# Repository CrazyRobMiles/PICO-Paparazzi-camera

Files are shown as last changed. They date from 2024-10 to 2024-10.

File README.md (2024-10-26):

# PICO-Paparazzi-camera
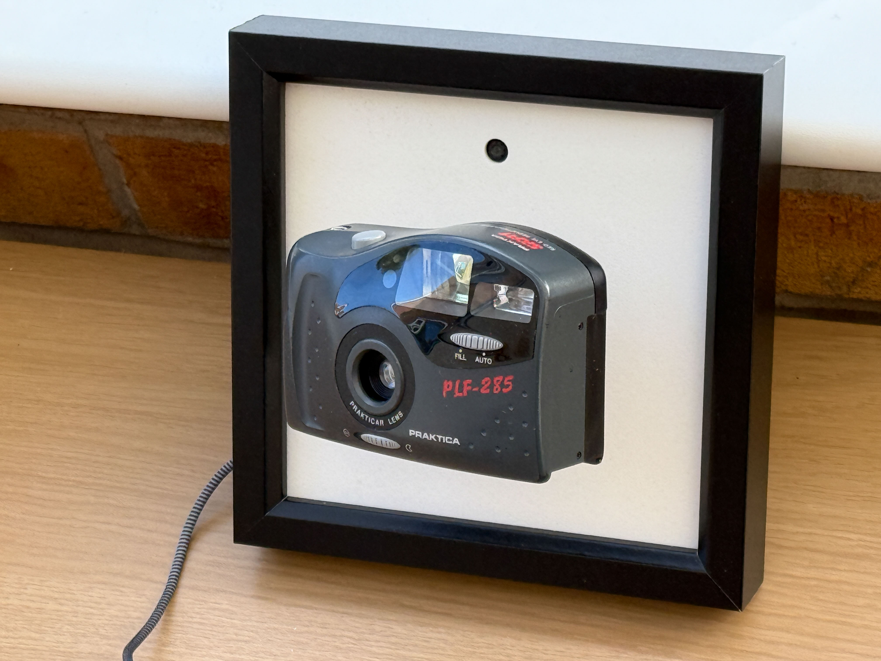
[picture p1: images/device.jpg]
Point and shoot camera floating above a picture frame

A camera that follows you around the room. Most of the time. 

This project started with a simple idea and then I found ways to make it more complicated. I had a lot of broken film cameras and 
I wanted to make something that made one follow me round the room. I found a sensor that can detect the position of people 
in front of it, and I started with a Raspberry Pi PICO and some servos to see if I could make something which pointed the 
servos at person. I called it the Paparazzi camera. If it went well the next step would be to make a larger 
installation with lots of cameras. It's been an interesting ride, and I'm still not sure if I've properly arrived, but it turns out 
that you can have a lot of fun with this stuff either way. The project is a work in progress and I've been through several iterations.
## Pan and tilt
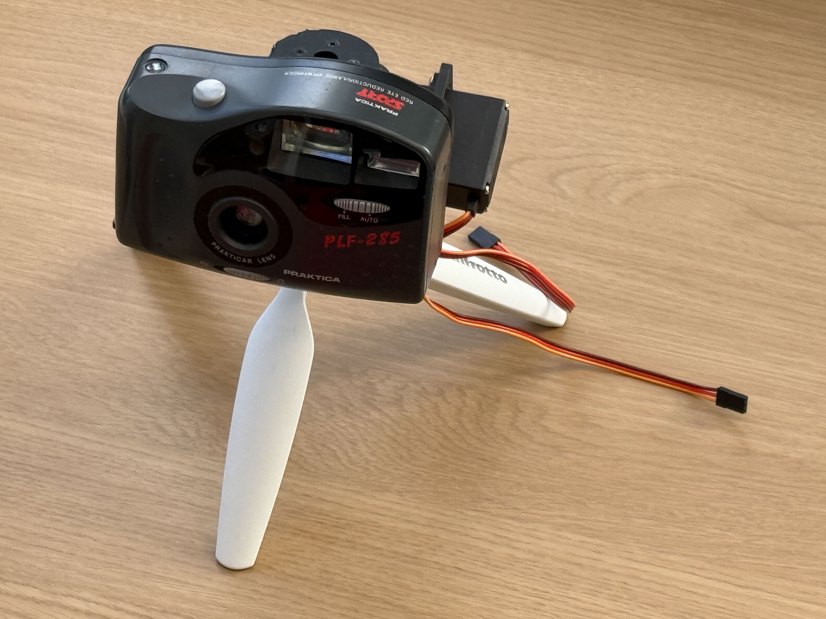
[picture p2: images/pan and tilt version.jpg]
pan and tilt mechanism


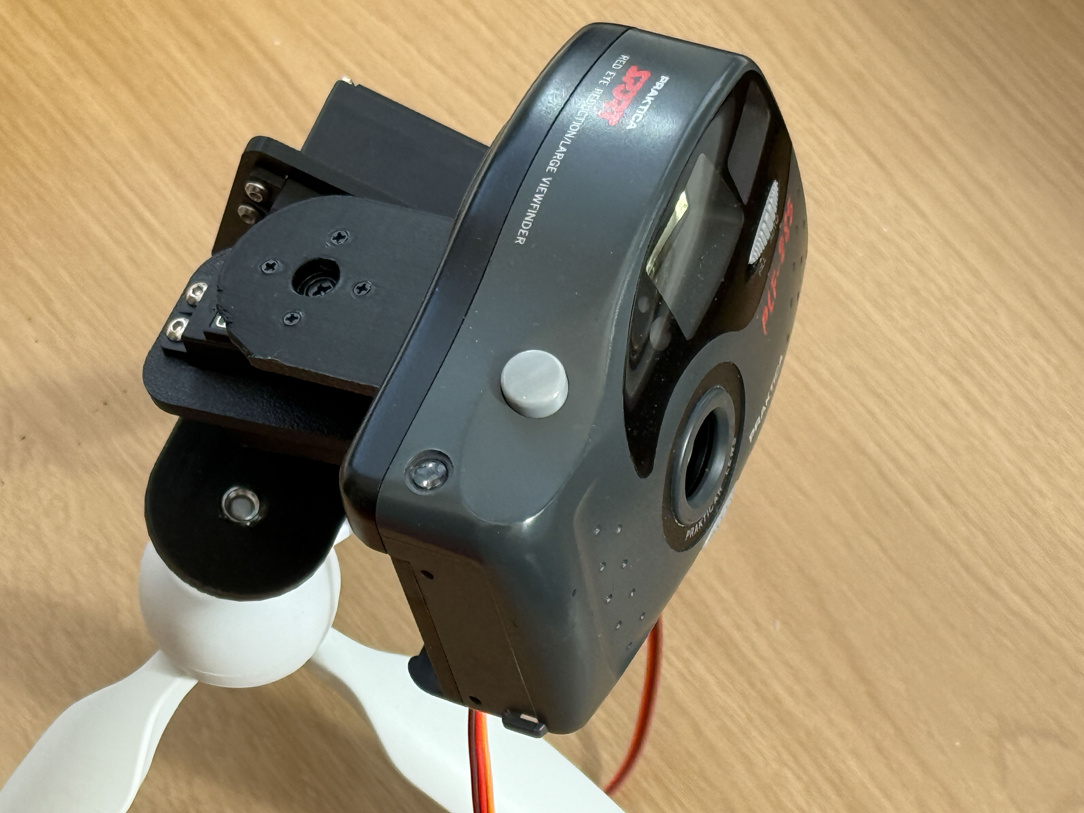
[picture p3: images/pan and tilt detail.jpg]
top view of pan and tilt


A pan and tilt mechanism was the first thing I made that could follow you with a camera. It uses two MG995 servos to create a pan and tilt mechanism. The camera rests on a support at the front. The mechanism 
works fine and will also support a smartphone (you can use it to shoot panoramas if you like).

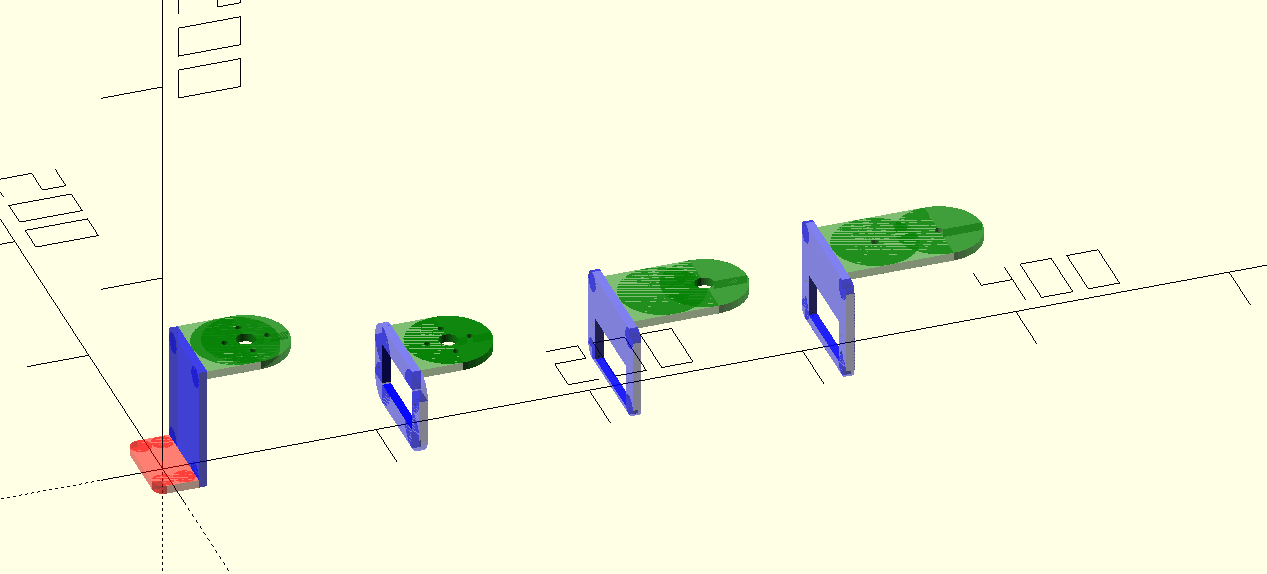
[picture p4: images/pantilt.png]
pan and tilt components

You can find the designs for these components in the 3d printing folder in this repository. Panning and tilting was fun but I really wanted something I could hang on the wall....
## Picture Camera mounting
So I moved on to a wall mounted device inside a six inch square picture frame. These are easy to get hold of from craft shops and are deep enough to allow electronics to be fitted in the back of the frame. Just make sure you get ones with removable glass. 
Some frames have the glass glued in, which makes it very had to remove without breaking it. You can see the picture frame version of the camera in the image at the top of this page. The camera seems to float out of the picture. 
At least, I think it does. 

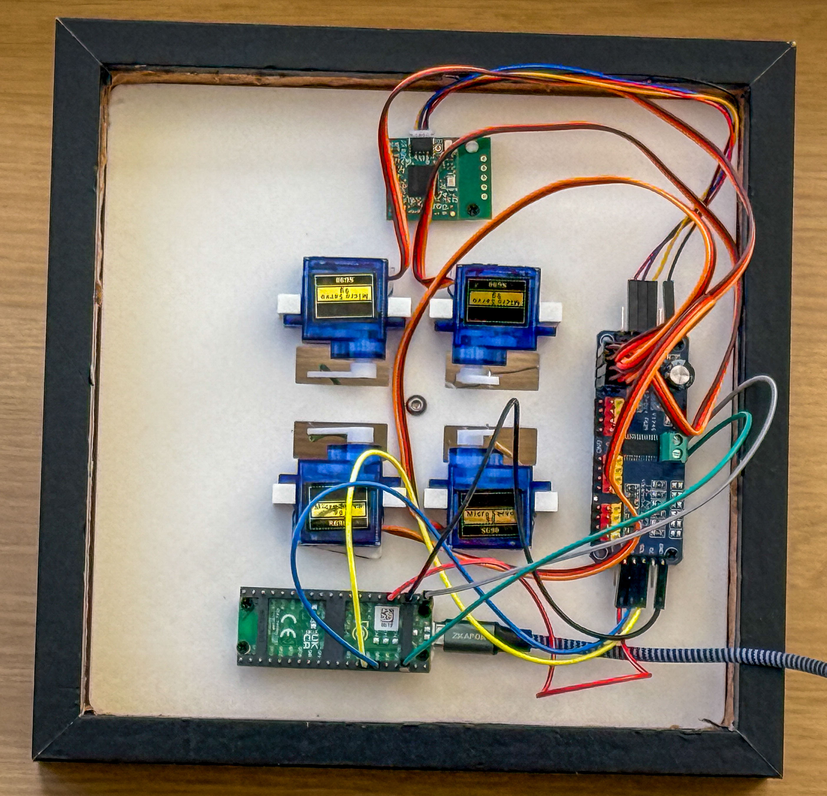
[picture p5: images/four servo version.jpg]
four servo version showing servos


This version uses a picture panel containing four tiny little servos, a Raspberry Pi PICO, a servo driver board and a Useful Sensors [Person sensor](https://github.com/usefulsensors/person_sensor_docs/blob/main/README.md). 

The camera is mounted on 3D printed ball and socket joint which is fitted inside the camera, ideally close to the camera's centre of balance. The idea is that the joint supports the weight of the camera, and the low powered servos only have to move the camera, not support its weight. To make sure there is enough movement force I used four stepper motors rather than two.

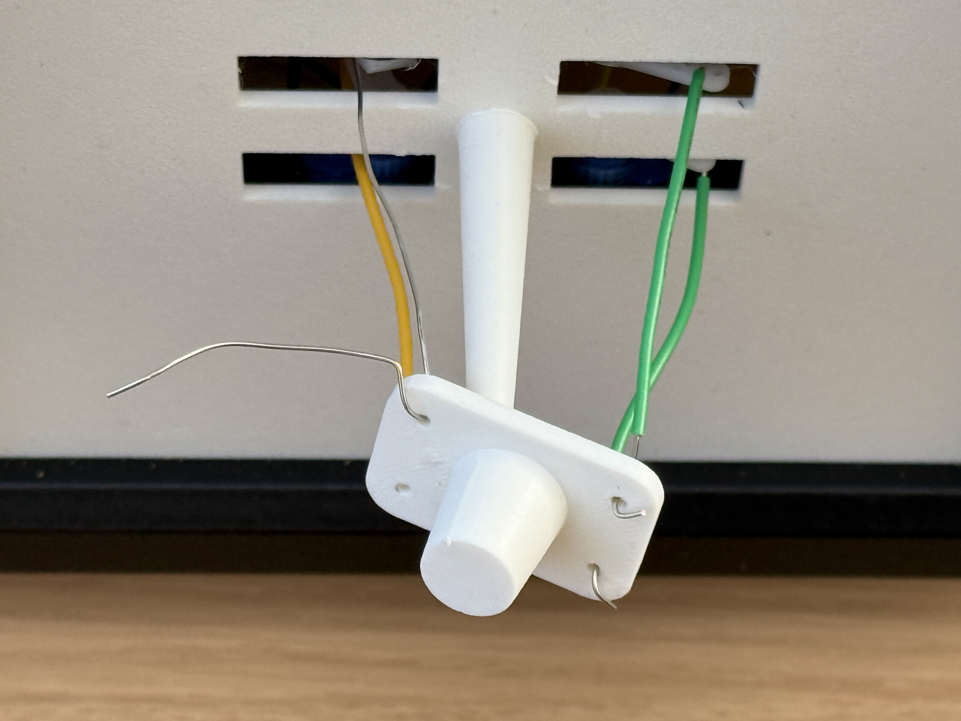
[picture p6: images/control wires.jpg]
control wires linking to the camera support


This shows how the control wires are connected from the servo horns to the camera support. 

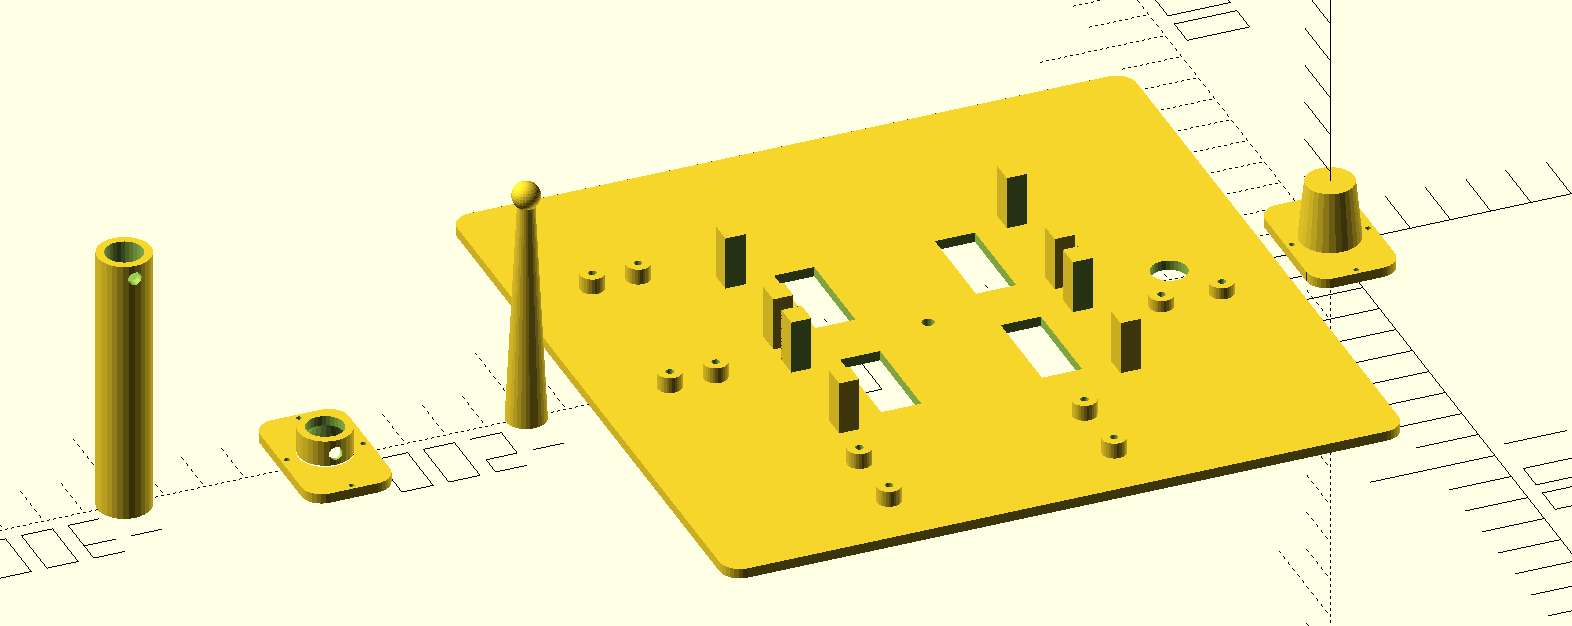
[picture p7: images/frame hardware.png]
3D printed parts for mounting servos


These are the 3D printable parts for the base, camera support pillar and the camera support. The servo motors fit between the support pillars and are glued into place. The camera fitting snaps onto the ball on top of the support. There are pillars to support the other components. There are also versions of the camera plate for a universal joint version of the camera support. The fittings are created by an OpenSCAD script you can find in the 3d printing folder. 

This version works quite well, but it has problems if the camera is not balanced correctly on the end of the support. This causes the camera to twist so that it is not horizontal. It also affects the way that the camera moves. If the camera is not balanced the small servos are unable to lift its weight.

So I thought I'd move on to make a version that uses more powerful servos that can lift the camera weight. I also switched to a universal joint rather than a ball and socket for the camera support. The joint provides pan and tilt motion but not twisting. You can find the universal joints that I used [here](https://www.amazon.co.uk/dp/B09NXJ9QF4).

## Two and Four servos

The four servo design uses SG90 servos. The two servo version of the design uses the same MG995 servos as the original pan and tilt mechanism. These can easily lift the camera up and down, although they are more heavily geared which means that the movement is slightly slower. The two servo backplate design is in the 3d printing folder. 

## Circuitry

The servos are driven by a PCA9685 16 Channel 12-bit PWM Servo motor driver. Both the servo driver board and the person sensor are connected to I2C. This is made easy by the way that the server driver board has i2c pass through. 

### Servo controller connection
The servo controller pins are connected as follows:

* scl GPIO5
* sda GPIO4

The power for the servos is obtained from the VBUS connection. This means that the servos are powered from the PICO USB connection. This is fine for the servos we are using, but if you start to use larger servos, heavier cameras or more servos you might want to consider 

### Servo connection for 2 servos
* Up/down - servo S0
* left/right - servo S1

### Servo connection for 4 servos

* Up - servo S0
* Left - servo S1
* Right - servo S2
* Down - servo S3

### The Person Sensor
The best way to connect the Person Sensor is by using a QWIIC connector brought out to four sockets which to to pins soldered onto the servo driver board. See the picture above for more details. 

The Person Sensor does work, although it can be a bit reticent. You need to make sure that the area where the camera is being used is well it and if clearing the background behind the image viewed by the sensor also improves recognition.

## Software

The software controlling the device is written in Circuit Python. It uses a set of AdaFruit libraries to control the servos. You can find the software and the libraries in the python folder. Just copy the contents of this folder onto the root directory of the storage for the Circuit Python drive which appears when the PICO is connected to the computer. The program is stored in a file called code.py and will run automatically when your PICO is powered up. When it starts up it moves the camera to each corner in turn and then back into the middle. 

### Servo configuration

You can select the servo configuration by changing the value on the first line of the code:
```
number_of_servos = 2
```
The number of servos can be 2 or 4. Any other number will cause an exception to be raised. 

### Paparazzi class

The Paparazzi class creates a PersonSensor object and an appropriate servo driver object. You can then repeatedly update the position of the camera by calling the update method on the Paparazzi instance:
```
pap = Paparazzi(number_of_servos)

while True:
    pap.update()
    time.sleep(0.1)

```
The code above updates the sensor every tenth of a second. You can use the scan method to test all the positions of the servos:

```
pap = Paparazzi(number_of_servos)

pap.scan()
```

This causes the program to scan the camera from left to right and up and down. It is very useful for tuning the lengths of the control wires.

Have fun!

Rob Miles

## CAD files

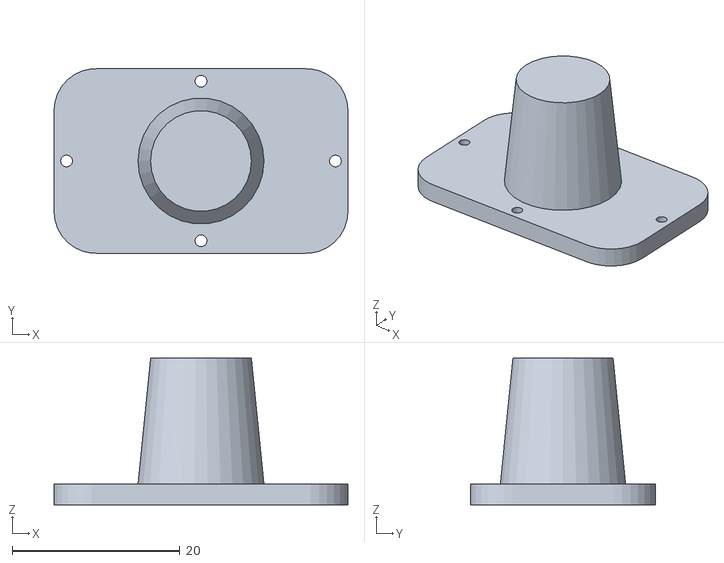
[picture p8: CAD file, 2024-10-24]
3d printing/frame/backplateSocket.stl
35.0 x 22.0 x 17.5

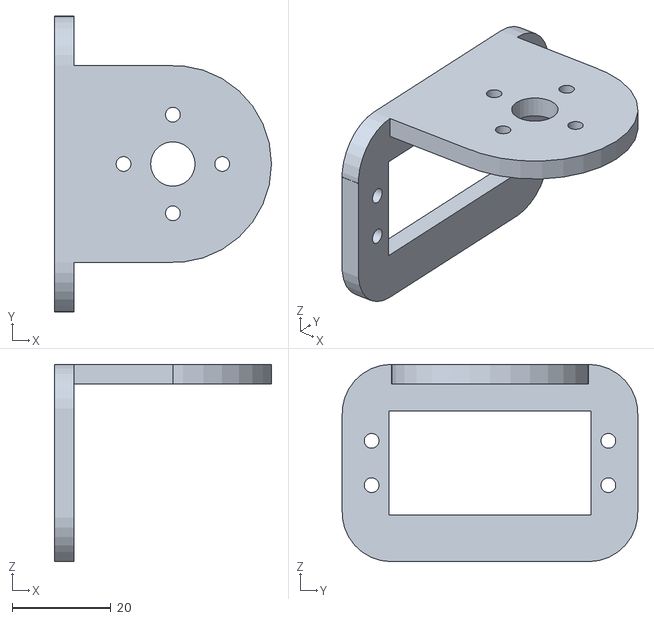
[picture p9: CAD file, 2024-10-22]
3d printing/pan tilt/TiltBracket.stl
44.0 x 60.0 x 40.0

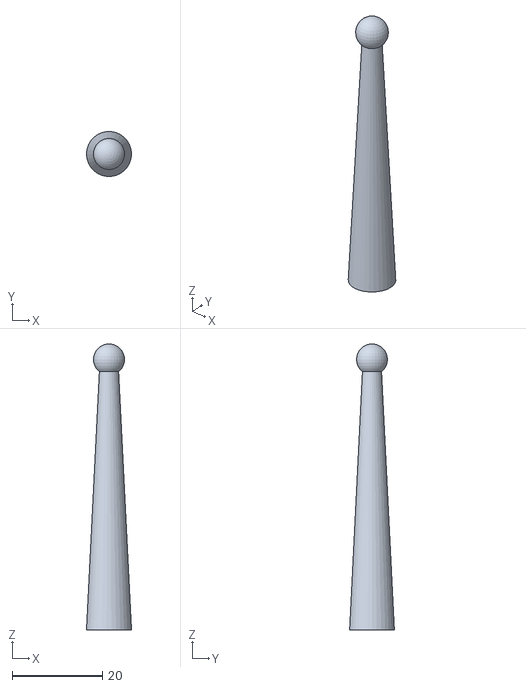
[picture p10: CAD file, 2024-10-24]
3d printing/frame/ballCentreSupport.stl
10.0 x 9.95 x 63.4

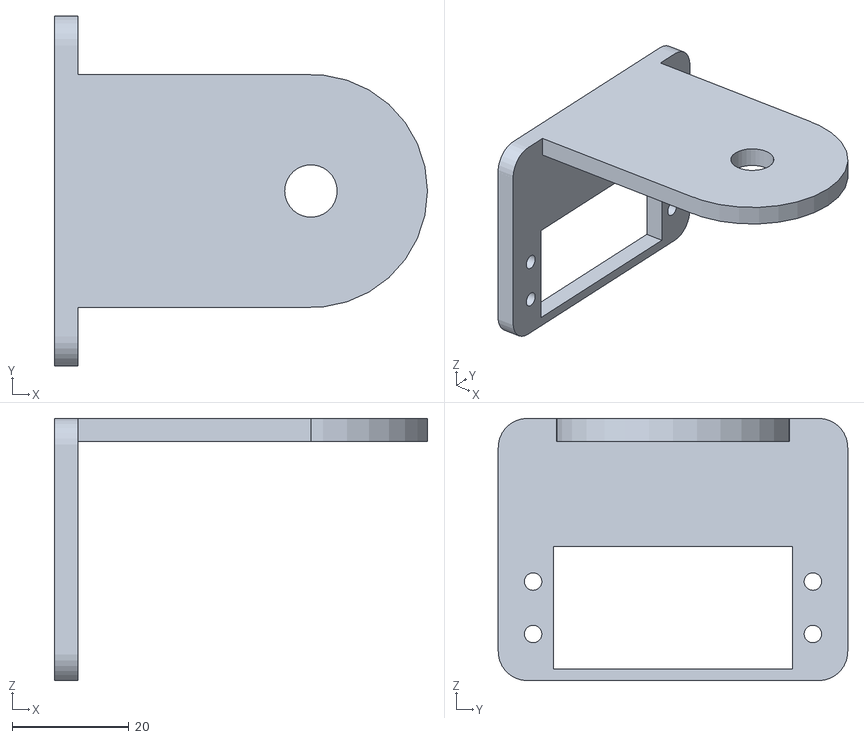
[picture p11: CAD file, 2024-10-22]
3d printing/pan tilt/tripodBracket.stl
64.0 x 60.0 x 45.0

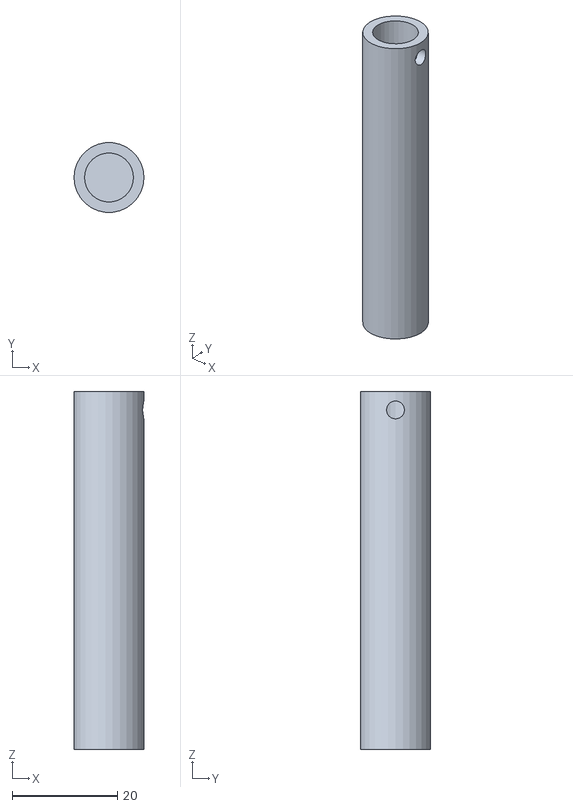
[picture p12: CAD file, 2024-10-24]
3d printing/frame/universalJointCentreSupport.stl
13.3 x 13.2 x 68.0

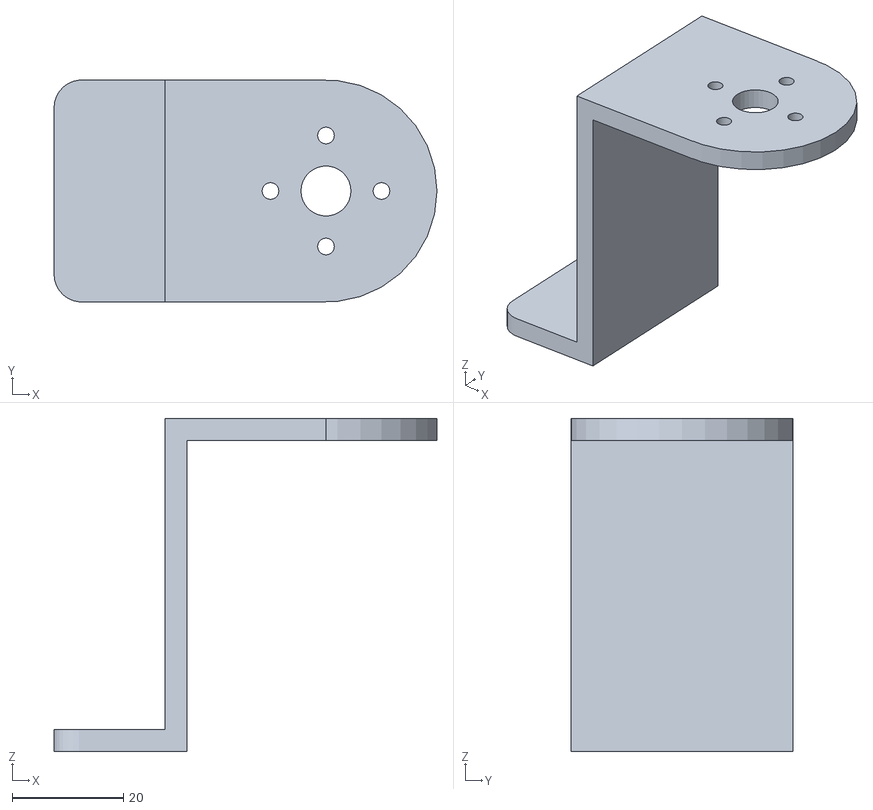
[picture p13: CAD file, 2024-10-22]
3d printing/pan tilt/CameraBracket.stl
69.0 x 40.0 x 60.0

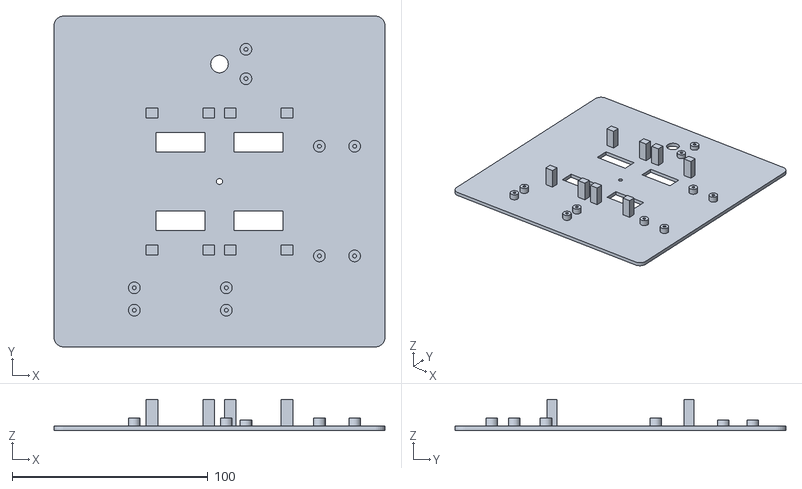
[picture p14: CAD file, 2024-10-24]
3d printing/frame/fourServoBackplate.stl
169.0 x 169.0 x 16.0

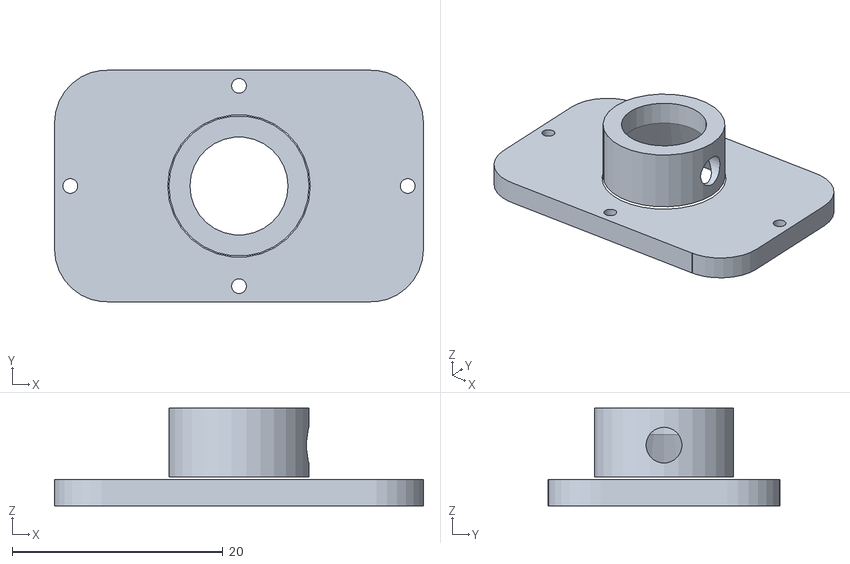
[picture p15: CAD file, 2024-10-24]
3d printing/frame/universalJointBackplate.stl
35.0 x 22.0 x 9.25

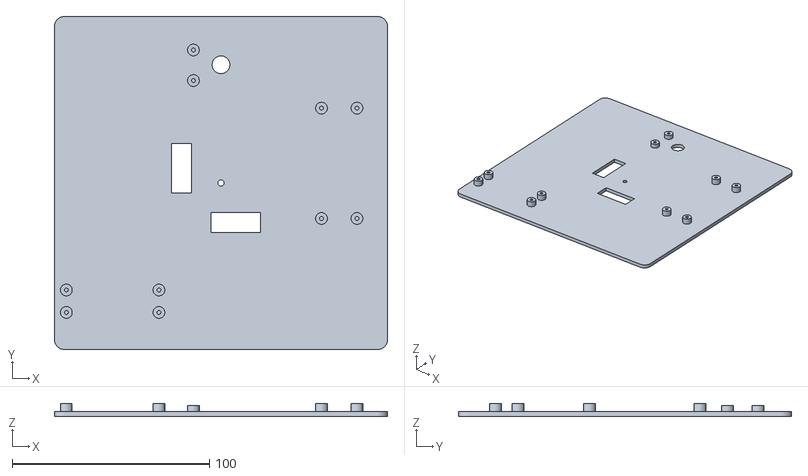
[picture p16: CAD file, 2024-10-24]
3d printing/frame/twoServoBackplate.stl
169.0 x 169.0 x 6.50

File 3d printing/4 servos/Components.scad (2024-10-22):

$fs=0.1;
extra = 0.5;

module box(width,depth,height){
    translate([-width/2.0, -depth/2.0, 0]){
        cube([width,depth,height]);
    }
}

module plate(width,depth,height, cornerRadius,corners)
{
    translate([-width/2.0, -depth/2.0, 0])
    {
        difference()
        {
            cube([width,depth,height]);
            if (corners[0]==1){
                translate([-extra,-extra,-extra])
                {
                     cube([cornerRadius+extra,cornerRadius+extra,height+2*extra]);
                }
            }
            if (corners[1]==1){
                translate([-extra,depth-cornerRadius,-extra])
                {
                    cube([cornerRadius+extra,cornerRadius+extra,height+2*extra]);
                }
            }
            if (corners[2]==1){
                translate([width-cornerRadius,depth-cornerRadius,-extra])
                { 
                    cube([cornerRadius+extra,cornerRadius+extra,height+2*extra]);
                }
            }
            if (corners[3]==1){
                translate([width-cornerRadius,-extra,-extra])
                {
                    cube([cornerRadius+extra,cornerRadius+extra,height+2*extra]);
                }
            }
        }
        translate([cornerRadius,cornerRadius,0]) cylinder(r=cornerRadius,h=height);
        translate([width-cornerRadius,cornerRadius,0]) cylinder(r=cornerRadius,h=height);
        translate([cornerRadius,depth-cornerRadius,0]) cylinder(r=cornerRadius,h=height);
        translate([width-cornerRadius,depth-cornerRadius,0]) cylinder(r=cornerRadius,h=height);
    }
}   

module fourHoles(width,depth,thickness,radius){
    x=width/2.0;
    y=depth/2.0;
    translate([-x,-y,-extra]) cylinder(h=thickness+(2*extra),r=radius);
    translate([x,y,-extra]) cylinder(h=thickness+(2*extra),r=radius);
    translate([-x,y,-extra]) cylinder(h=thickness+(2*extra),r=radius);
    translate([x,-y,-extra]) cylinder(h=thickness+(2*extra),r=radius);
}

module fourHolesCross(width,depth,thickness,radius){
    x=width/2.0;
    y=depth/2.0;
    translate([-x,-0,-extra]) cylinder(h=thickness+(2*extra),r=radius);
    translate([x,0,-extra]) cylinder(h=thickness+(2*extra),r=radius);
    translate([0,y,-extra]) cylinder(h=thickness+(2*extra),r=radius);
    translate([0,-y,-extra]) cylinder(h=thickness+(2*extra),r=radius);
}

module fourSlots(width,depth,thickness,slotWidth,slotDepth){
    x=width/2.0 ;
    y=depth/2.0 ;
    translate([-slotWidth/2.0, -slotDepth/2.0,0]) {
        translate([-x,-y,-extra]) cube([slotWidth,slotDepth,thickness+(2*extra)]);
        translate([-x,y,-extra]) cube([slotWidth,slotDepth,thickness+(2*extra)]);
        translate([x,-y,-extra]) cube([slotWidth,slotDepth,thickness+(2*extra)]);
        translate([x,y,-extra]) cube([slotWidth,slotDepth,thickness+(2*extra)]);
    }
}    
    
module fourSlotsCross(width,depth,thickness,slotWidth,slotDepth){
    x=width/2.0 ;
    y=depth/2.0 ;
    translate([-slotWidth/2.0, -slotDepth/2.0,0]) {
        translate([-x,0,-extra]) cube([slotWidth,slotDepth,thickness+(2*extra)]);
        translate([x, 0,-extra]) cube([slotWidth,slotDepth,thickness+(2*extra)]);
        translate([0,-y,-extra]) cube([slotWidth,slotDepth,thickness+(2*extra)]);
        translate([0,y,-extra]) cube([slotWidth,slotDepth,thickness+(2*extra)]);
    }
}    



module fourMountingHoles(width,depth,thickness,sideHeight,radius){
    x=width/2.0 ;
    y=depth/2.0 ;
    z = thickness+(sideHeight/2.0);
    
    translate([-x,y,-extra]) cylinder(r=radius,h=sideHeight,center=true);
}


plateWidth=35;
plateDepth=22;
cornerRadius=5.0;
cornerHoleInset = 10.0;
cornerHoleRadius = 1.0;
centreHoleRadius = 3.5;
centreSupportWidth = 4.0;
centerSupportHeight = 15.0;
cameraHoleInset = 15.0;
plateThickness = 2.5;

backplateCornerHoleInset = 3;
backplateCornerHoleRadius = 0.7;

module backplate(){
    difference(){
        union(){
            plate(plateWidth,plateDepth,plateThickness,cornerRadius,[1,1,1,1]);
            translate([0,0,plateThickness]) cylinder(r1=centreHoleRadius+centreSupportWidth,r2=centreHoleRadius+centreSupportWidth-1.5,h=centerSupportHeight);
        }
        fourHolesCross(plateWidth-backplateCornerHoleInset,plateDepth-backplateCornerHoleInset,plateThickness,backplateCornerHoleRadius);
        translate([0,0,centerSupportHeight-centreHoleRadius]) sphere(r=centreHoleRadius);
        cylinder(h=10,r1=8,r2=centreHoleRadius-0.45);
    }
}

servoSlotWidth=10;
servoShotDepth=25;
backPlateWidth=169;
backPlateDepth=169;
servoMountSpacing = 28;
servoAxisOffset = 20;
servoBlockDepth=4;
servoFixingHoleRadius=1;
servoPillarThickness=13;
servoOffsetFromHole=30;
servoOffsetFromAxis=5;
servoOuterDepth=35.0;
servoBodyDepth=23.0;
servoMountDepth=5.0;

supportCornerHoleRadius = 1.5;
supportCornerHoleInset=2.5;
baseWidth=40;

servoInset=30.0;

servoAreaWidth=40;
servoAreaDepth=40;

pillarHoleTopRadius=3.0;
pillarHoleBottomRadius = 3.5;
pillarHoleRadius = 1.55;

personSensorWidth = 28;
personSensorDepth = 22;
sensorUnitWidth=20;
sensorHoleSpacing=18;
personSensorHoleInset=3.5;
 
cameraHoleRadius = 4.5;
personSensorYPos = 60;
personSensorPillarRadius = 3;
personSensorPillarHoleRadius = 1.0;
personSensorPillerHeight=3;

module pillar(height,pillarRadius,holeRadius){
    difference(){
        cylinder(h=height,r=pillarRadius);
        cylinder(h=height,r=holeRadius);
    }
}

module mountingPillars(xSpacing,ySpacing,pillarHeight,pillarRadius, pillarHoleRadius){
    x=xSpacing/2;
    y=ySpacing/2;
    translate([-x,-y,0]) pillar(pillarHeight,pillarRadius,pillarHoleRadius);
    translate([-x,y,0]) pillar(pillarHeight,pillarRadius,pillarHoleRadius);
    translate([x,-y,0]) pillar(pillarHeight,pillarRadius,pillarHoleRadius);
    translate([x,y,0]) pillar(pillarHeight,pillarRadius,pillarHoleRadius);
}

module addServo(plate,thickness){
    union(plate){
        translate([0,0,thickness]){
            difference(){
                box(servoPillarThickness,servoOuterDepth,servoMountDepth);
                box(servoPillarThickness,servoBodyDepth,servoMountDepth);
            }
        }
    }
}


module servoPlate(){
    
    difference(){
        union(){
            plate(backPlateWidth,backPlateDepth,plateThickness,cornerRadius,[1,1,1,1]);
            translate([0,0,plateThickness]){
                difference(){
                    fourSlots(servoAreaWidth,servoAreaDepth+servoOffsetFromHole,servoPillarThickness,servoOuterDepth,servoMountDepth);
                    fourSlots(servoAreaWidth,servoAreaDepth+servoOffsetFromHole,servoPillarThickness,servoBodyDepth,servoMountDepth);
                }
            }
            translate([(personSensorWidth/2)-personSensorHoleInset+3,personSensorYPos+(personSensorDepth/2.0)-personSensorHoleInset,plateThickness]){
                pillar(personSensorPillerHeight, personSensorPillarRadius, personSensorPillarHoleRadius);
                translate([0,-(personSensorDepth-(2*personSensorHoleInset)),0]){
                    pillar(personSensorPillerHeight, personSensorPillarRadius, personSensorPillarHoleRadius);
                }
            }
            
            translate([-20,-60,plateThickness]){
                mountingPillars(47,11.4,4,3,1);
                translate([80,50,0]){
                    mountingPillars(18,56,4,3,1);
                }
            }
        }
        
        cylinder(h=plateThickness,r=pillarHoleRadius);

        fourSlots(servoAreaWidth,servoAreaDepth,plateThickness,servoShotDepth,servoSlotWidth);
        
        translate([sensorUnitWidth-personSensorWidth+8,personSensorYPos,0])cylinder(h=plateThickness,r=cameraHoleRadius);
    }

}

module fullServoPlate()
{
    
    plate(backPlateWidth,backPlateDepth,plateThickness,cornerRadius,[1,1,1,1]);
    
    
}

supportBaseRadius = 15;
rodwidth=60;
rodRadius=2.0;
rodSphereRadius = 3.45;
rodScrewHoleRadius = 1.4;
rodScrewHoleHeight = 10;


module centreSupport(){
    difference(){
        union(){
            cylinder(h=rodwidth,r1=rodRadius+3,r2=rodRadius);
            translate([0,0,rodwidth]){
                sphere(r=rodSphereRadius);
            }
        }
        cylinder(h=rodScrewHoleHeight,r1=rodScrewHoleRadius+0.1,r2=rodScrewHoleRadius);
    }
}

ujRadius=4.65;
ujHeight=6.0;
sleeveThickness=2.0;
grubScrewHeight=2.5;
grubScrewRadius = 1.7;

module universalSupport(){
    difference(){
        // Make the outer cylinder
        cylinder(h=ujHeight+sleeveThickness,r=ujRadius++sleeveThickness);
        translate([0,0,sleeveThickness])cylinder(h=ujHeight,r=ujRadius);
        translate([0,0,grubScrewHeight+sleeveThickness]){
            rotate([0,90,0]){
                cylinder(h=ujRadius+sleeveThickness,r=grubScrewRadius);
            }
        }
    }
}
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

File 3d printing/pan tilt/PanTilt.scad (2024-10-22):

$fs=0.1;
extra = 0.5;


module box(width,depth,height){
    translate([-width/2.0, -depth/2.0, 0]){
        cube([width,depth,height]);
    }
}

module plate(width,depth,height, cornerRadius,corners)
{
    translate([-width/2.0, -depth/2.0, 0])
    {
        difference()
        {
            cube([width,depth,height]);
            if (corners[0]==1){
                translate([-extra,-extra,-extra])
                {
                     cube([cornerRadius+extra,cornerRadius+extra,height+2*extra]);
                }
            }
            if (corners[1]==1){
                translate([-extra,depth-cornerRadius,-extra])
                {
                    cube([cornerRadius+extra,cornerRadius+extra,height+2*extra]);
                }
            }
            if (corners[2]==1){
                translate([width-cornerRadius,depth-cornerRadius,-extra])
                { 
                    cube([cornerRadius+extra,cornerRadius+extra,height+2*extra]);
                }
            }
            if (corners[3]==1){
                translate([width-cornerRadius,-extra,-extra])
                {
                    cube([cornerRadius+extra,cornerRadius+extra,height+2*extra]);
                }
            }
        }
        translate([cornerRadius,cornerRadius,0]) cylinder(r=cornerRadius,h=height);
        translate([width-cornerRadius,cornerRadius,0]) cylinder(r=cornerRadius,h=height);
        translate([cornerRadius,depth-cornerRadius,0]) cylinder(r=cornerRadius,h=height);
        translate([width-cornerRadius,depth-cornerRadius,0]) cylinder(r=cornerRadius,h=height);
    }
}   

module cameraBracket()
{
    cameraTabWidth = 20;
    backHeight = 60;
    tabDepth = 40;
    servoPadWidth = 45;
    thickness = 4;
    cornerRadius = 5;
    servoHoleRadius = 4.5;
    servoFittingHoleRadius = 1.5;
    fittingoffset = 10.0;
    union(){
        color("red",0.5){
            plate(cameraTabWidth,tabDepth,thickness,cornerRadius,[1,1,0,0]);
        }
        color("blue",0.5){
            translate([cameraTabWidth/2.0,0,backHeight/2.0]){
                rotate(90,[0,1,0]){
                    plate(backHeight,tabDepth,thickness,cornerRadius,[0,0,0,0]);
                }
            }
        }
        color("green",0.5){
            union(){
                translate([servoPadWidth/2.0+cameraTabWidth/2.0+thickness,0,backHeight-thickness]){
                    difference(){
                        plate(servoPadWidth,tabDepth,thickness,tabDepth/2.0,[0,0,1,1]);
                        translate([servoPadWidth/2.0-tabDepth/2.0,0,-extra]){
                            cylinder(h=thickness+(2*extra),r=servoHoleRadius);
                            translate([-fittingoffset,0,0]) cylinder(h=thickness+(2*extra),r=servoFittingHoleRadius);
                            translate([fittingoffset,0,0]) cylinder(h=thickness+(2*extra),r=servoFittingHoleRadius);
                            translate([0,-fittingoffset,0]) cylinder(h=thickness+(2*extra),r=servoFittingHoleRadius);
                            translate([0,fittingoffset,0]) cylinder(h=thickness+(2*extra),r=servoFittingHoleRadius);
                        }
                    }
                }
            }
        }
    }
}

module tiltBracket(){
    tiltTabWidth = 20;
    backHeight = 40;
    tabDepth = 60;
    servoPadDepth = 40;
    servoPadWidth = 40;
    thickness = 4;
    cornerRadius = 10;
    servoHoleRadius = 4.5;
    servoFittingHoleRadius = 1.5;
    servoHoleWidth = 21.0;
    servoHoleDepth = 41.0;
    fittingoffset = 10.0;
    servoHoleWidthSpacing = 9;
    servoHoleDepthSpacing = 48;
    union(){
        color("blue",0.5){
            translate([tiltTabWidth/2.0,0,backHeight/2.0]){
                rotate(90,[0,1,0]){
                    difference(){
                        plate(backHeight,tabDepth,thickness,cornerRadius,[1,1,1,1]);
                        translate([0,0,-extra]){
                            plate(servoHoleWidth,servoHoleDepth,thickness+2*extra,1,[0,0,0,0]);
                            x = servoHoleWidthSpacing/2.0;
                            y = servoHoleDepthSpacing/2.0;
                            translate([-x,-y,0]) cylinder(h=thickness+(2*extra),r=servoFittingHoleRadius);
                            translate([x,y,0]) cylinder(h=thickness+(2*extra),r=servoFittingHoleRadius);
                            translate([-x,y,0]) cylinder(h=thickness+(2*extra),r=servoFittingHoleRadius);
                            translate([x,-y,0]) cylinder(h=thickness+(2*extra),r=servoFittingHoleRadius);
                        }
                    }
                }
            }
        }
        color("green",0.5){
            union(){
                translate([servoPadWidth/2.0+tiltTabWidth/2.0+thickness,0,backHeight-thickness]){
                    difference(){
                        plate(servoPadWidth,servoPadDepth,thickness,servoPadDepth/2.0,[0,0,1,1]);
                        translate([servoPadWidth/2.0-servoPadDepth/2.0,0,-extra]){
                            cylinder(h=thickness+(2*extra),r=servoHoleRadius);
                            translate([-fittingoffset,0,0]) cylinder(h=thickness+(2*extra),r=servoFittingHoleRadius);
                            translate([fittingoffset,0,0]) cylinder(h=thickness+(2*extra),r=servoFittingHoleRadius);
                            translate([0,-fittingoffset,0]) cylinder(h=thickness+(2*extra),r=servoFittingHoleRadius);
                            translate([0,fittingoffset,0]) cylinder(h=thickness+(2*extra),r=servoFittingHoleRadius);
                        }
                    }
                }
            }
        }
    }
}

module tripodBracket(){
    tiltTabWidth = 20;
    backHeight = 45;
    tabDepth = 60;
    servoPadDepth = 40;
    servoPadWidth = 60;
    thickness = 4;
    cornerRadius = 5;
    servoHoleRadius = 4.5;
    servoFittingHoleRadius = 1.5;
    servoHoleWidth = 21.0;
    servoHoleDepth = 41.0;
    fittingoffset = 10.0;
    servoHoleWidthSpacing = 9;
    servoHoleDepthSpacing = 48;
    union(){
        color("blue",0.5){
            translate([tiltTabWidth/2.0,0,backHeight/2.0]){
                rotate(90,[0,1,0]){
                    difference(){
                        plate(backHeight,tabDepth,thickness,cornerRadius,[1,1,1,1]);
                        translate([10,0,-extra]){
                            plate(servoHoleWidth,servoHoleDepth,thickness+2*extra,1,[0,0,0,0]);
                            x = servoHoleWidthSpacing/2.0;
                            y = servoHoleDepthSpacing/2.0;
                            translate([-x,-y,0]) cylinder(h=thickness+(2*extra),r=servoFittingHoleRadius);
                            translate([x,y,0]) cylinder(h=thickness+(2*extra),r=servoFittingHoleRadius);
                            translate([-x,y,0]) cylinder(h=thickness+(2*extra),r=servoFittingHoleRadius);
                            translate([x,-y,0]) cylinder(h=thickness+(2*extra),r=servoFittingHoleRadius);
                        }
                    }
                }
            }
        }
        color("green",0.5){
            union(){
                translate([servoPadWidth/2.0+tiltTabWidth/2.0+thickness,0,backHeight-thickness]){
                    difference(){
                        plate(servoPadWidth,servoPadDepth,thickness,servoPadDepth/2.0,[0,0,1,1]);
                        translate([servoPadWidth/2.0-servoPadDepth/2.0,0,-extra]){
                            cylinder(h=thickness+(2*extra),r=servoHoleRadius);
                        }
                    }
                }
            }
        }
    }
}
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

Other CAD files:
3d printing/frame/Components.scad

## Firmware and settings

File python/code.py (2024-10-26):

number_of_servos = 2

import time
import board
import busio
import struct
from adafruit_pca9685 import PCA9685
from adafruit_motor import servo
import random

SERVO_MIN_ANGLE = 0   # Minimum angle for the servos
SERVO_MAX_ANGLE = 180  # Maximum angle for the servos
NEUTRAL_ANGLE = 90     # Neutral angle for flat plate

def clamp(value, min_value, max_value):
    """Clamp the value between min_value and max_value."""
    return max(min_value, min(value, max_value))

class ServoManager():

    def __init__(self, i2c,no_of_servos):

        self.pca = PCA9685(i2c)

        # Set the PWM frequency to 60hz.
        self.pca.frequency = 60
        
        self.servos = []
        for no in range(0,no_of_servos):
            self.servos.append(servo.Servo(self.pca.channels[no]))
    
    def set_servo_angles(self,x, y, max_tilt_angle=60):
        """
        Given X and Y coordinates (in some desired range, e.g., -1 to 1), this function
        calculates the servo angles for four servos controlling the corners of the plate.
        
        Args:
            x (float): Desired X direction (from -1 to 1).
            y (float): Desired Y direction (from -1 to 1).
            max_tilt_angle (float): Maximum tilt angle for the servos in any direction.
            
        """
        
        # Clamp X and Y to the range [-1, 1]
        x = clamp(x, -1, 1)
        y = clamp(y, -1, 1)

        # Calculate the tilt contribution from X and Y direction
        x_tilt = max_tilt_angle * x
        y_tilt = max_tilt_angle * y
        
        upDownAngle = NEUTRAL_ANGLE + (y*max_tilt_angle)
        leftRightAngle = NEUTRAL_ANGLE + (x*max_tilt_angle)
        
        self.set_positions(upDownAngle,leftRightAngle)
        
    # Scans the camera over the entire scene
    # Used for calibration
    def scan(self):
        while True:
            for y in range(-10,11):
                for x in range(-10,11):
                    xs=x/10.0
                    ys=y/10.0
                    self.set_servo_angles(xs,ys)
                    time.sleep(0.1)

    def startup_test(self):
        tests = ((-1,-1),(1,-1),(1,1), (-1,1),(0,0))
        for pos in tests:
            (x,y)=pos
            self.set_servo_angles(x,y)
            time.sleep(1)
            
        
    def manual_set(self):
        print("Enter servo and change value")
        command = input()
        (servo,change)= command.split()
        if servo<len(self.servos):
            print("Servo:",servo,"Change",change)
            val = self.servos[servo].value
            self.servos[servo].value = val + change
            print("Value set")
        else:
            print("Servo out of range")
        
class ServoManager4(ServoManager):
    
    def __init__(self, i2c):
    
        # physical servo arrangement:
        #    0
        # 1      2
        #    3
        # each servo is connected to a side of the camera holder
        
        super(ServoManager4,self).__init__(i2c, 4)

        
    def set_positions(self,x,y):
        self.servos[1].angle = x;
        self.servos[2].angle = 180-x;
        self.servos[0].angle = y;
        self.servos[3].angle = 180-y;

class ServoManager2(ServoManager):
    
    def __init__(self, i2c):
        # physical servo arrangement:
        #    0
        # 1
        # each servo is connected to a side of the camera holder
        super(ServoManager2,self).__init__(i2c, 2)

    def set_positions(self,v0,v1):
        self.servos[0].angle = v0
        self.servos[1].angle = v1
        
class PersonSensor():

    # The person sensor has the I2C ID of hex 62, or decimal 98.
    PERSON_SENSOR_I2C_ADDRESS = 0x62
      
    # We will be reading raw bytes over I2C, and we'll need to decode them into
    # data structures. These strings define the format used for the decoding, and
    # are derived from the layouts defined in the developer guide.
    PERSON_SENSOR_I2C_HEADER_FORMAT = "BBH"
    PERSON_SENSOR_I2C_HEADER_BYTE_COUNT = struct.calcsize(
        PERSON_SENSOR_I2C_HEADER_FORMAT)

    PERSON_SENSOR_FACE_FORMAT = "BBBBBBbB"
    PERSON_SENSOR_FACE_BYTE_COUNT = struct.calcsize(PERSON_SENSOR_FACE_FORMAT)

    PERSON_SENSOR_FACE_MAX = 4
    PERSON_SENSOR_RESULT_FORMAT = PERSON_SENSOR_I2C_HEADER_FORMAT + \
        "B" + PERSON_SENSOR_FACE_FORMAT * PERSON_SENSOR_FACE_MAX + "H"
    PERSON_SENSOR_RESULT_BYTE_COUNT = struct.calcsize(PERSON_SENSOR_RESULT_FORMAT)

    def __init__(self, i2c):
        self.i2c = i2c
    
    def get_faces(self):
        
        while not self.i2c.try_lock():
            pass
        
        read_data = bytearray(self.PERSON_SENSOR_RESULT_BYTE_COUNT)
        self.i2c.readfrom_into(self.PERSON_SENSOR_I2C_ADDRESS, read_data)
        self.i2c.unlock()

        offset = 0
        (pad1, pad2, payload_bytes) = struct.unpack_from(
            self.PERSON_SENSOR_I2C_HEADER_FORMAT, read_data, offset)
        offset = offset + self.PERSON_SENSOR_I2C_HEADER_BYTE_COUNT

        (num_faces) = struct.unpack_from("B", read_data, offset)
        num_faces = int(num_faces[0])
        offset = offset + 1

        faces = []
        for i in range(num_faces):
            (box_confidence, box_left, box_top, box_right, box_bottom, id_confidence, id,
             is_facing) = struct.unpack_from(self.PERSON_SENSOR_FACE_FORMAT, read_data, offset)
            offset = offset + self.PERSON_SENSOR_FACE_BYTE_COUNT
            face = {
                "box_confidence": box_confidence,
                "box_left": box_left,
                "box_top": box_top,
                "box_right": box_right,
                "box_bottom": box_bottom,
                "id_confidence": id_confidence,
                "id": id,
                "is_facing": is_facing,
            }
            faces.append(face)
        checksum = struct.unpack_from("H", read_data, offset)
        return faces
        
class Paparazzi():
    
    def __init__(self, number_of_servos):    
        print("Getting I2C")
        i2c = busio.I2C(scl=board.GP5, sda=board.GP4)    # Pi Pico RP2040

        print("Getting Servo Manager")
        if number_of_servos == 2:
            self.servoManager = ServoManager2(i2c)
        elif number_of_servos == 4: 
            self.servoManager = ServoManager4(i2c)
        else:
            raise ValueError("Invalid number of servos")

        print("Getting person sensor")
        self.personSensor = PersonSensor(i2c)

                 
    # Updates the sensor position
    def update(self):
        faces = self.personSensor.get_faces()
        if len(faces)>0:
            face = faces[0]
    #        print(face)
    #        print("    Left X: ",face["box_left"],"Top Y:",face["box_top"] )
            x = face["box_left"] + (face["box_right"] -face["box_left"])/2.0
            y = face["box_top"] + (face["box_bottom"] - face["box_top"])/2.0
    #        print("    Orig X: ", x,"Orig Y:",y )
            width = face["box_right"] - face["box_left"]
            height = face["box_bottom"] - face["box_top"]
            # scale for the servo control
            sx = (x-128)/128
            sy = (y-128)/128
            
            print("    SX:", sy, " SY:", sy)
            self.servoManager.set_servo_angles(sx,sy)
            #print("    X: ", x,"Y:",y,"width:",width,"height:",height)
            
    def scan(self):
        self.servoManager.scan()
        

pap = Paparazzi(number_of_servos)

# call this to scan the camera through all positions
# Good for testing
#pap.servoManager.scan()

# Moves the camera around the four corners 
pap.servoManager.startup_test()

while True:
    pap.update()
    time.sleep(0.1)



        
            

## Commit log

2024-10-22 Alpha release
    [CameraBracket.stl, Components.scad, PanTilt.scad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]
2024-10-24 First release
    [Components.scad, backplateSocket.stl, ballCentreSupport.stl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]
2024-10-26 Added code auto run and power on self test
